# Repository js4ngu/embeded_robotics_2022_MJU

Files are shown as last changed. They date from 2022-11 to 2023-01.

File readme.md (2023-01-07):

# 2022-2학기 명지대학교 임베디드 로보틱스 수업
* 3 DOF 메뉴플레이터 설계 및 개발
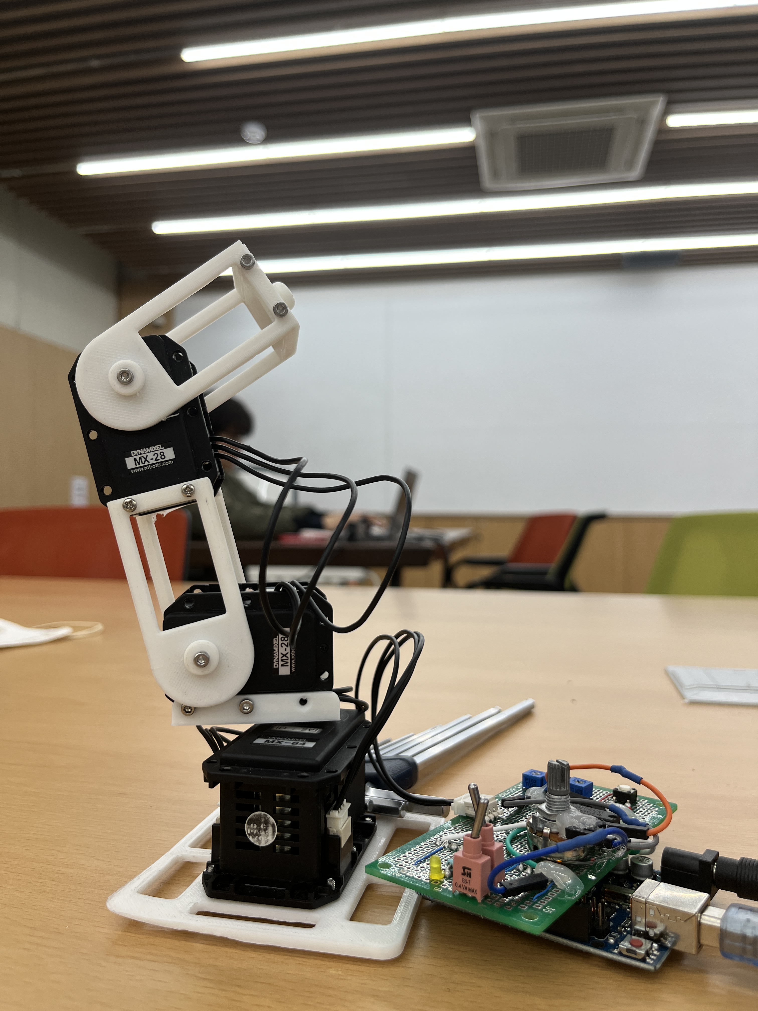
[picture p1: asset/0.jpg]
* 
* https://youtu.be/WQkYmM9BQwU
* 역기학모드
  * 직교좌표계로 좌를 입력하면 Endpoint가 해당 좌표로 이동
  * 문제를 쉽게 해석하기 위해 직교좌표계를 원통좌표계로 변환 $\phi$ 정보를 첫번째 관절에 제공
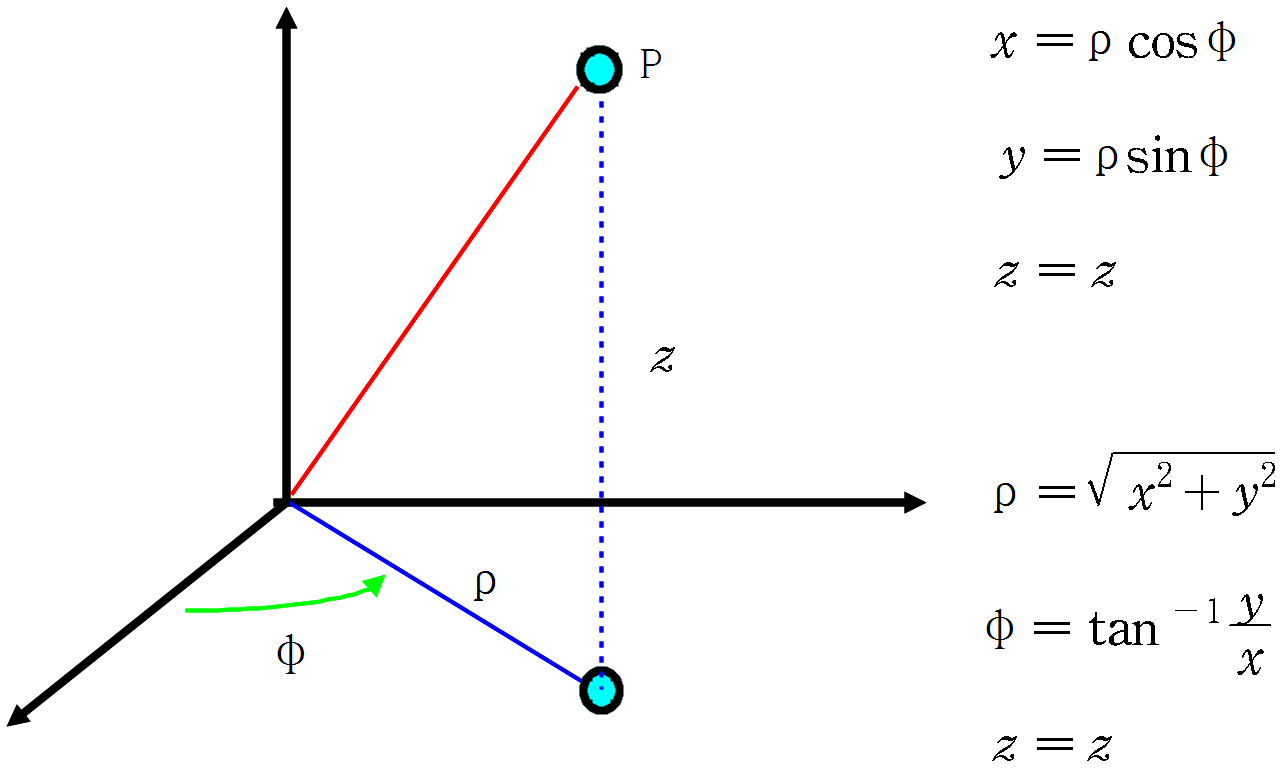
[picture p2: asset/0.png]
cord
  * 
  * $r$과 $z$로 이뤄진 2차원 평면상에서 도해적으로 해석
    * 본인은 $\rho$ 대신 $r$문자 사용
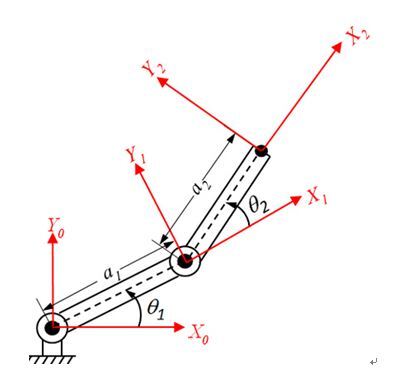
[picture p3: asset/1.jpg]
  * 
  * 결과는 아래와 같음
  * th1
  * th2
  * $\theta_1$은 $theta_2$에 dependency가 있음
  * 즉, 직교좌표계 $\rightarrow$ 원통좌표계 $\rightarrow$ $\theta_2$ $\rightarrow$ $\theta_1$ 순으로 계산해야함
  * 코드로 구현하면 아래와 같음
  * ```cpp
    void cartsia2cylinder(double x, double y, double _z){
        double cord[3];
        pi = atan2(y,x) * 57.2958;
        r = sqrt(x*x + y*y);
        z = _z;
    }

    double findTheta2(double r, double z){
        double innerSqrt = ((L1 + L2)*(L1 + L2) - (r*r + z*z))/
                            ((r*r + z*z) - (L1 - L2)*(L1 - L2));
        return 2*atan(sqrt(innerSqrt))* 57.2958;
    }

    double findTheta1(double r, double z, double th2){
        double firstTerm = atan2(z,r)*57.2958;
        double secondTerm = atan2(L2*sin(th2),(L1 + L2*cos(th2)))* 57.2958;
        return firstTerm - secondTerm;
    }
    ```
  * 여차저차 $\theta_1$, $\theta_2$ 구해서 다이나믹셀에 전해주면 끝~
* POT 모드
  * 포텐셜 미터 값 읽어서 각관절 구동~
  
 ## Report
 [[임베디드로보틱스]_6조_유종상_60171851.pdf](https://github.com/js4ngu/embeded_robotics_2022_MJU/files/10366018/_6._._60171851.pdf)

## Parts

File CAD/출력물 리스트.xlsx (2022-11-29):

Part | Required | STL Convert | G-CODE Convert | 3D printing
 |  |  |  | 1 | 2
28Tzig_50mm.par | 2 | O | O
28Tzig_50mm_right.par | 2 | O
robot_part_3.par | 2 | O
robot_part_4.par | 1 | O
robot_part_5.par | 1 | O
robot_part_6.par | 1 | O
robot_part_7.par | 1 | O
robot_part_8.par | 1 | O
robot_part_9.par | 1 | O
robot_part_10.par | 0 | O

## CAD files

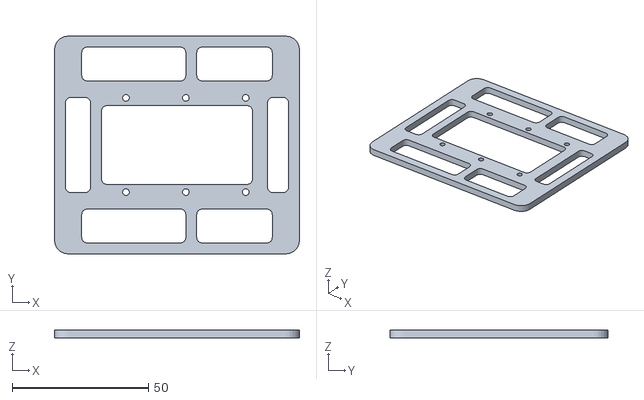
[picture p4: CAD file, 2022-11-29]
CAD/STL/robot_part_9.stl
90.0 x 80.0 x 3.00

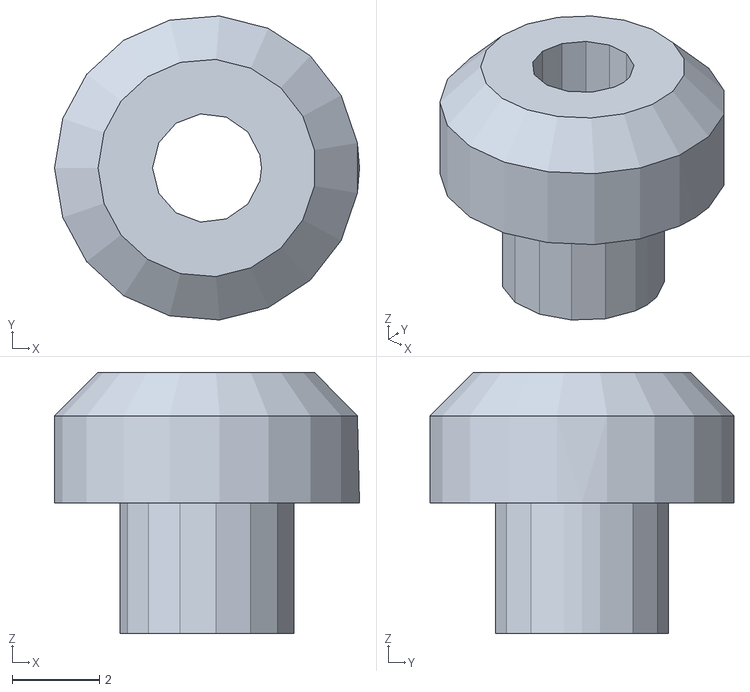
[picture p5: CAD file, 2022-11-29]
CAD/STL/robot_part_3.stl
7.00 x 6.98 x 6.00

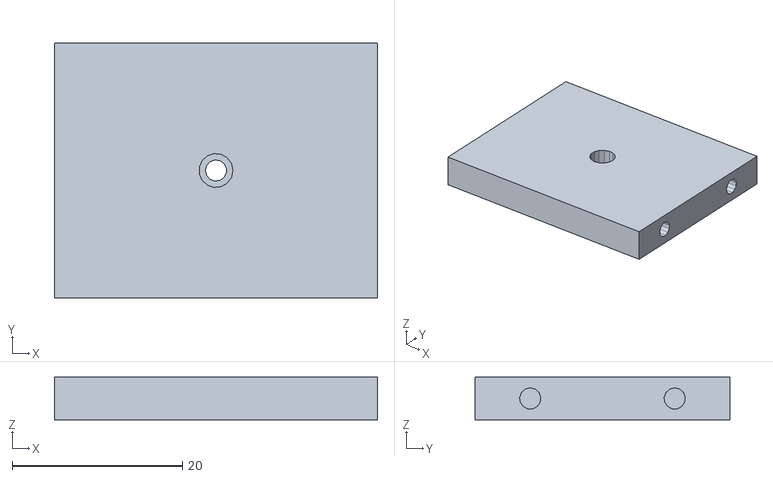
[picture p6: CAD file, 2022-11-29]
CAD/STL/robot_part_6.stl
38.0 x 30.0 x 5.00

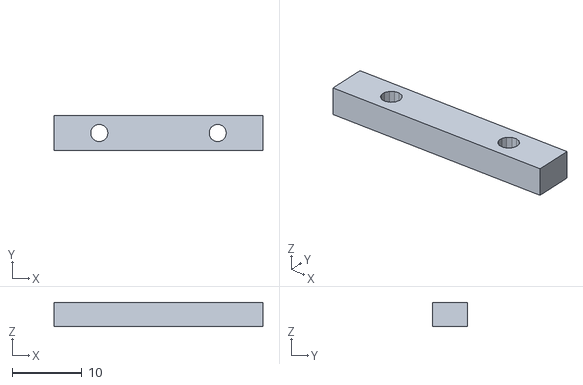
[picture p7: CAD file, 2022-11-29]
CAD/STL/robot_part_4.stl
30.0 x 5.00 x 3.50

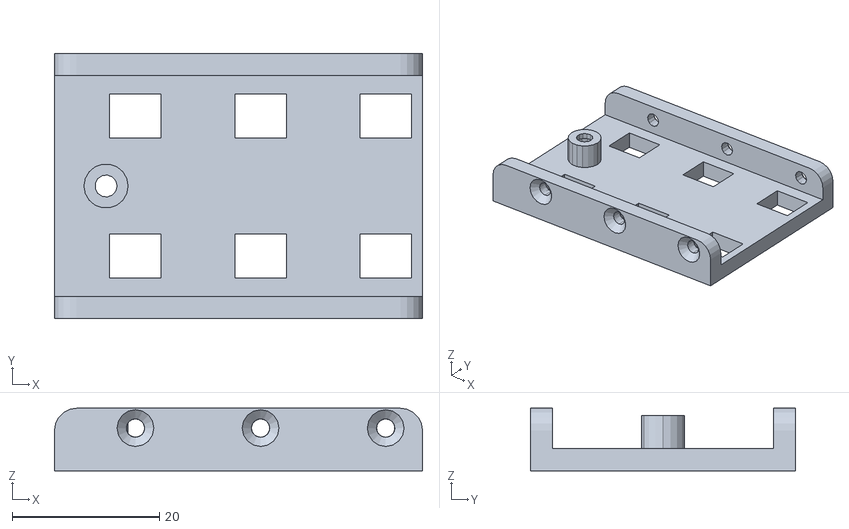
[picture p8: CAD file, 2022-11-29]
CAD/STL/robot_part_8.stl
50.0 x 36.0 x 8.50

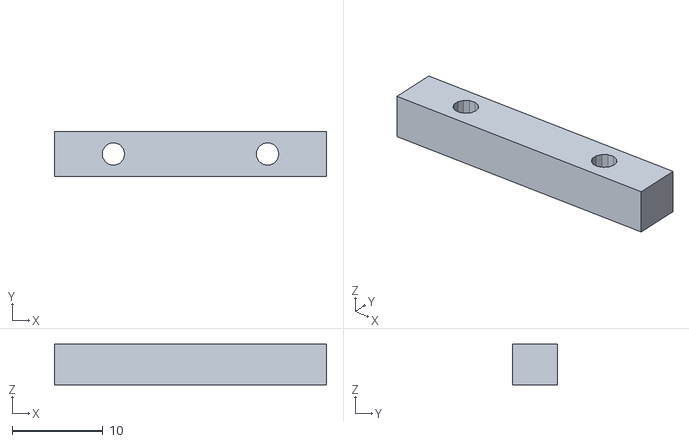
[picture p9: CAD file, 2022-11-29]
CAD/STL/robot_part_5.stl
30.0 x 5.00 x 4.50

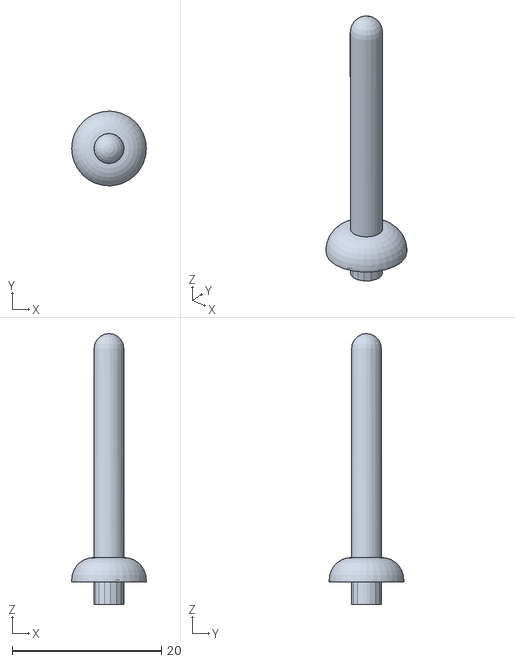
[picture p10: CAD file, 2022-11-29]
CAD/STL/robot_part_7.stl
10.0 x 10.0 x 36.3

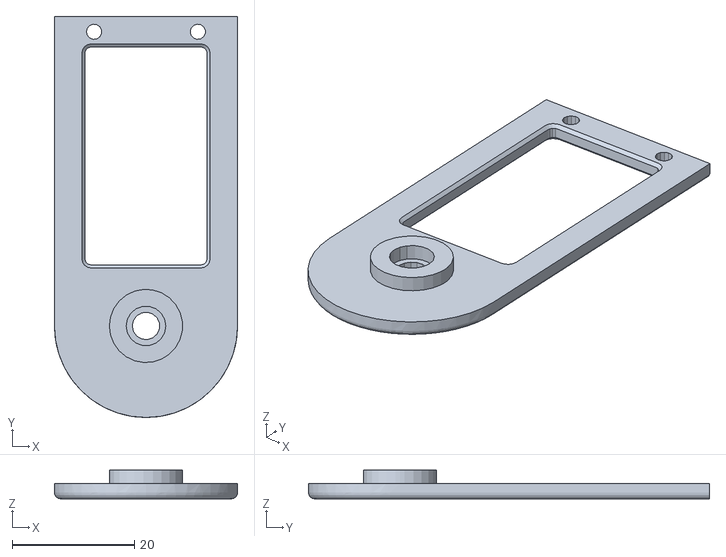
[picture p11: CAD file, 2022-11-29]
CAD/STL/28Tzig_50mm_right.stl
30.0 x 65.7 x 4.70

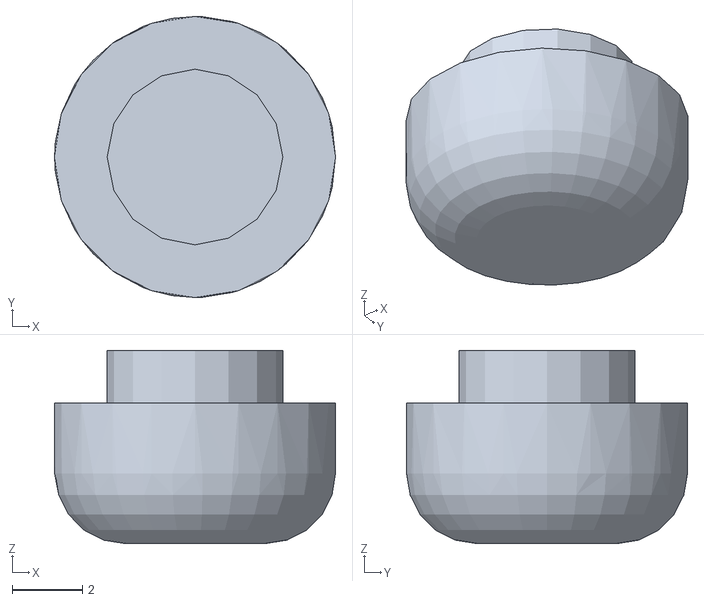
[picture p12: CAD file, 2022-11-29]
CAD/STL/robot_part_10.stl
8.00 x 8.00 x 5.50

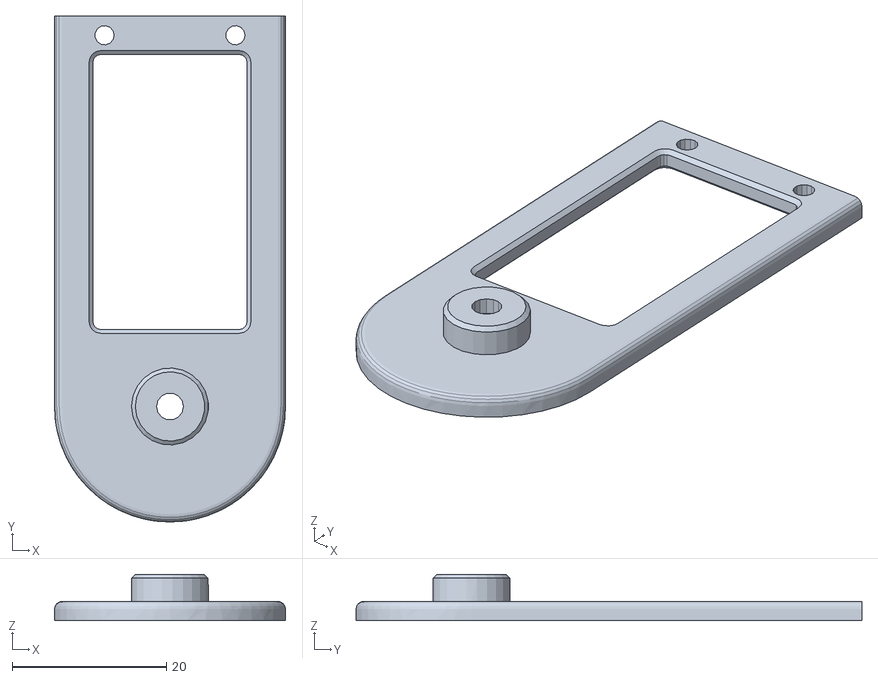
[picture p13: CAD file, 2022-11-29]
CAD/STL/28Tzig_50mm.stl
30.0 x 65.7 x 6.00

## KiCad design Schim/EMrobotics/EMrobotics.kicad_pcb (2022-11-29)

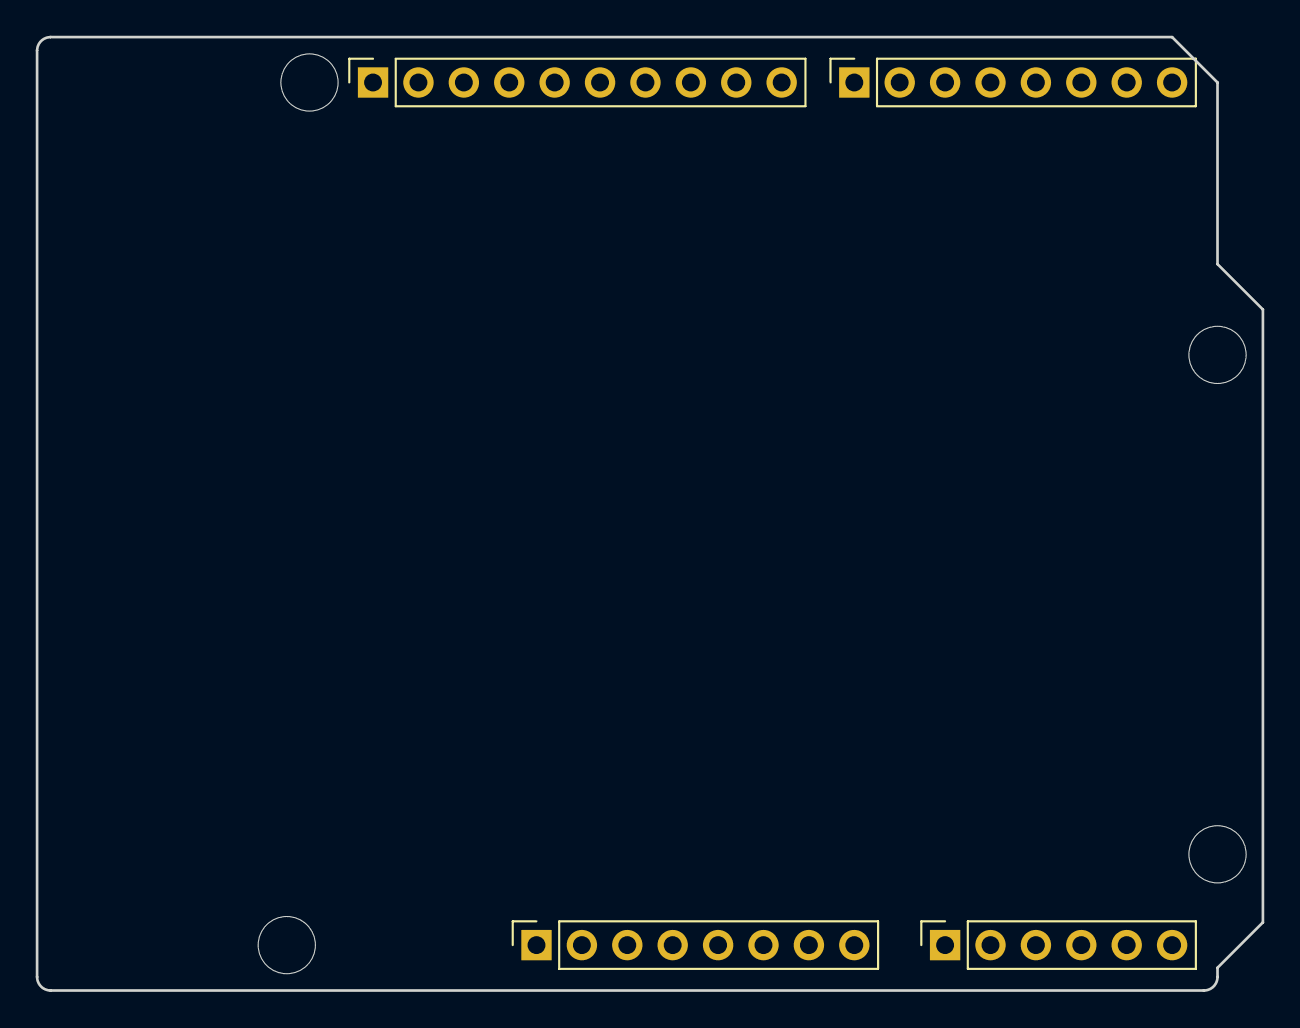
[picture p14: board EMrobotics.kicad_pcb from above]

Board: 2 copper layers, 68.6 x 53.3 mm, 8 parts (0 on the bottom side), 3 nets, no tracks yet.

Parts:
J1: Power; PinSocket_1x08_P2.54mm_Vertical
J2: Digital/PWM; PinSocket_1x10_P2.54mm_Vertical
J3: Analog; PinSocket_1x06_P2.54mm_Vertical
J4: Digital/PWM; PinSocket_1x08_P2.54mm_Vertical
MH1, MH2, MH3, MH4: MountingHole_3.2mm

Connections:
/SCL/A5: J2.1, J3.6
/SDA/A4: J2.2, J3.5
GND: J1.6, J1.7, J2.4

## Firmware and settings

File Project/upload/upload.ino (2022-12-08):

#include <stdio.h>
#include <stdlib.h>
#include <math.h>
#define L1 35
#define L2 35
#define BUFFER_SIZE 10
#define TX_Enable_pin            12  // 송신 활성화 핀
#define RX_Enable_pin            13  // 수신 활성화 핀
#define POTMODE                  0
#define INVERSEKINEMATICMODE     1
#define MOTOR_TEST_MODE          2
#define MOTOR_INIT_MODE          3
#define BOTTOM_ID                0
#define MIDDLE_ID                1
#define TOP_ID                   100
#define POT_BOTTOM               0
#define POT_MIDDLE               1
#define POT_TOP                  2
#define ERROR                    -1
typedef enum _com_mode {
    RX_MODE,
    TX_MODE
} com_mode;

// 통신 모드(송/수신)에 따른 버퍼칩 설정
void set_com_mode(com_mode mode);
// 통신 프로토콜에 체크섬 삽입
void dx_insert_checksum_byte(unsigned char *packet);
// id 설정을 위한 통신 패킷 조립
void dx_set_id(unsigned char id);
// 제어 모드 설정
// 정방향과 역방향 최대 각도에 따라 바퀴모드나 관절모드로 설정됨
// 바퀴모드: 모두 0으로 설정
// 관절모드: 0~360(0xfff)로 설정
void dx_set_control_mode(unsigned char id, unsigned char cw_angle_limit[2], unsigned char ccw_angle_limit[2]);
// 위치제어용 패킷 조립
void dx_tx_packet_for_position_control(unsigned char id, unsigned char goal_pos[2]);
int readModeSW();
void potMode();
void inverseMode();
void cartsia2cylinder(float x, float y, float _z);
float findTheta2(float r, float z);
float findTheta1(float r, float z, float th2);
void findInverseKinematic(float x, float y, float z);
bool toggleSW();
unsigned char topPacket(int REF);
unsigned char bottomPacket(int REF);

unsigned char ref_0[2];
unsigned char ref_1[2];
unsigned char ref_2[2];
int potVal[3];
float cartsianCord[3];
float r, pi, z;
int motorDeg[3];
char buf[BUFFER_SIZE];
int stateMainFSM;

void setup() {
    Serial.begin(57600);  // 통신 속도
    pinMode(TX_Enable_pin, OUTPUT); //TX Enable
    pinMode(RX_Enable_pin, OUTPUT); //RX Enable
    pinMode(2, OUTPUT);
    pinMode(5, OUTPUT);
    pinMode(6, OUTPUT);
    pinMode(8, OUTPUT);
    pinMode(9, INPUT);
    pinMode(10, INPUT);

    unsigned char cw_angle_limit[2];
    unsigned char ccw_angle_limit[2];

    cw_angle_limit[0] = 0x00;
    cw_angle_limit[1] = 0x00;
    ccw_angle_limit[0] = 0xFF;
    ccw_angle_limit[1] = 0xFF;  

    dx_set_control_mode(254, cw_angle_limit, ccw_angle_limit);
    digitalWrite(2, HIGH);
    digitalWrite(6, HIGH);
    digitalWrite(8, HIGH);
    delay(1);
}

void loop() {
    switch (readModeSW()) {
    case POTMODE:
        potMode();
        break;

    case INVERSEKINEMATICMODE:
        inverseMode();
        break;

    case MOTOR_TEST_MODE:
        ref_0[0] = 0x00;
        ref_0[1] = 0x10;
        dx_tx_packet_for_position_control(BOTTOM_ID, ref_0);
        delay(1000);
        dx_tx_packet_for_position_control(MIDDLE_ID, ref_0);
        delay(1000);
        dx_tx_packet_for_position_control(TOP_ID, ref_0);
        delay(1000);
        ref_0[0] = 0x00;
        ref_0[1] = 0x00;
        dx_tx_packet_for_position_control(BOTTOM_ID, ref_0);
        delay(1000);
        dx_tx_packet_for_position_control(MIDDLE_ID, ref_0);
        delay(1000);
        dx_tx_packet_for_position_control(TOP_ID, ref_0);
        delay(1000);
        break;

    case MOTOR_INIT_MODE:
        ref_0[0] = 0x00;
        ref_0[1] = 0x08;
        dx_tx_packet_for_position_control(BOTTOM_ID, ref_0);
        delay(1000);
        dx_tx_packet_for_position_control(MIDDLE_ID, ref_0);
        delay(1000);
        dx_tx_packet_for_position_control(TOP_ID, ref_0);
        delay(1000);
        while(1);
    }
}

int readModeSW(){
    bool modeSW = digitalRead(9);
    if(modeSW == 0){
        digitalWrite(5, HIGH);
        return POTMODE;
    }
    else if(modeSW == 1){
        digitalWrite(5, LOW);
        return INVERSEKINEMATICMODE;
    }
    else
        return ERROR;
}

bool toggleSW(){
    static bool prev_btn;
    static bool current_btn;
    current_btn = digitalRead(10);
    if ( (prev_btn ^ current_btn) == 1){
        prev_btn = current_btn;
        Serial.println("SW");
        return 1;
    }
    else{
        prev_btn = current_btn;
        return 0;
    }
}

void potMode(){
    static int state = 0;
    switch (state)
    {
    case 0:
        while(1){
            potVal[POT_BOTTOM] = analogRead(A2)*4;
            Serial.print("POT_BOTTOM : ");
            Serial.println(potVal[POT_BOTTOM]);
            if (toggleSW() == 1) {
                state = 1;
                break;
            }
        }
        break;
    case 1:
        while(1){
            potVal[POT_MIDDLE] = analogRead(A2)*4;
            Serial.print("POT_MIDDLE : ");
            Serial.println(potVal[POT_MIDDLE]);
            if (toggleSW() == 1) {
                state = 2;
                break;
            }
        }
        break;
    case 2:
        while(1){
            potVal[POT_TOP] = analogRead(A2)*4;
            Serial.print("POT_TOP : ");
            Serial.println(potVal[POT_TOP]);
            if (toggleSW() == 1) {
                state = 3;
                break;
            }
        }
        break;
    case 3:
        Serial.print(potVal[POT_BOTTOM]);
        Serial.print("\t");
        Serial.print(potVal[POT_MIDDLE]);
        Serial.print("\t");
        Serial.println(potVal[POT_TOP]);
        state = 4;
        break;

    case 4:
        motorDeg[POT_BOTTOM] = potVal[POT_BOTTOM];
        motorDeg[POT_MIDDLE] = potVal[POT_MIDDLE];
        motorDeg[POT_TOP]    = potVal[POT_TOP];

        ref_0[0] = bottomPacket(motorDeg[0]);
        ref_0[1] = topPacket(motorDeg[0]);
        dx_tx_packet_for_position_control(BOTTOM_ID, ref_0);
        delay(1000);
        ref_1[0] = bottomPacket(motorDeg[1]);
        ref_1[1] = topPacket(motorDeg[1]);
        dx_tx_packet_for_position_control(MIDDLE_ID, ref_1);
        delay(1000);
        ref_2[0] = bottomPacket(motorDeg[2]);
        ref_2[1] = topPacket(motorDeg[2]);
        dx_tx_packet_for_position_control(TOP_ID, ref_2);
        delay(1000);

        while (1) {
            if (toggleSW() == 1) {
                state = 0;
                break;
            }
        }    
        break;
    }
}

void set_com_mode(com_mode mode) {

  if (mode == RX_MODE)
  {
    // 비활성화 먼저 수행하여 동시에 활성화 되는 순간을 방지
    digitalWrite(TX_Enable_pin, LOW); // TX disable
    digitalWrite(RX_Enable_pin, HIGH); // RX Enable
  }
  else
  {
    // 비활성화 먼저 수행하여 동시에 활성화 되는 순간을 방지
    digitalWrite(RX_Enable_pin, LOW); // RX disable
    digitalWrite(TX_Enable_pin, HIGH); // TX Enable
  }
}
void dx_insert_checksum_byte(unsigned char *packet) {

  unsigned char i;
  unsigned char checksum_pt;
  unsigned char checksum;
  unsigned char packet_length;

  packet_length = packet[3];  // 3번 바이트에 패킷 길이가 저장되어 있음
  checksum_pt = packet_length + 3;

  checksum = 0x00;
  for (i = 2; i < checksum_pt; i++) {
    checksum += packet[i];
  }
  packet[checksum_pt] = ~checksum;

}
void dx_set_id(unsigned char id) {
  unsigned char packet[8];
  unsigned char i;

  packet[0] = 0xFF;
  packet[1] = 0xFF;
  packet[2] = 0xFE;
  packet[3] = 0x04;
  packet[4] = 0x03;
  packet[5] = 0x03;
  packet[6] = id;

  dx_insert_checksum_byte(packet);

  set_com_mode(TX_MODE); // 송신 모드로 설정
  for (i = 0; i < 8; i++) {
    Serial.write(packet[i]);
  }

  // 송신완료시까지 블록
  while ( !(UCSR0A & (1 << TXC0)) ) {
    __asm__("nop\n\t"); // no operation
  }

  set_com_mode(RX_MODE); // 수신 모드로 설정

}
void dx_set_control_mode(unsigned char id,
                         unsigned char cw_angle_limit[2],
                         unsigned char ccw_angle_limit[2]) {

  unsigned char packet[11];
  unsigned char i;

  packet[0] = 0xFF;
  packet[1] = 0xFF;
  packet[2] = id;
  packet[3] = 0x07;
  packet[4] = 0x03;
  packet[5] = 0x06;
  packet[6] = cw_angle_limit[0];
  packet[7] = cw_angle_limit[1];
  packet[8] = ccw_angle_limit[0];
  packet[9] = ccw_angle_limit[1];
  dx_insert_checksum_byte(packet);

  set_com_mode(TX_MODE); // 송신 모드로 설정
  for (i = 0; i < 11; i++) {
    Serial.write(packet[i]);
  }

  // 송신완료시까지 블록
  while ( !(UCSR0A & (1 << TXC0)) ) {
    __asm__("nop\n\t"); // no operation
  }

  set_com_mode(RX_MODE); // 수신 모드로 설정

}
void dx_tx_packet_for_position_control(unsigned char id, unsigned char goal_pos[2]) {
  
  unsigned char packet[11];
  unsigned char i;

  packet[0] = 0xFF;
  packet[1] = 0xFF;
  packet[2] = id;
  packet[3] = 0x07;
  packet[4] = 0x03;
  packet[5] = 0x1E;
  packet[6] = goal_pos[0];
  packet[7] = goal_pos[1];
  packet[8] = 0x00;
  packet[9] = 0x00;
  dx_insert_checksum_byte(packet);

  set_com_mode(TX_MODE); // 송신 모드로 설정
  for (i = 0; i < 11; i++) {
    Serial.write(packet[i]);
  }

  // 송신완료시까지 블록
  while ( !(UCSR0A & (1 << TXC0)) ) {
    __asm__("nop\n\t"); // no operation
  }
  
  set_com_mode(RX_MODE); // 수신 모드로 설정
}

void findInverseKinematic(float x, float y, float z){
    cartsia2cylinder(x, y, z);
    float theta2 = findTheta2(r,z);
    float theta1 = findTheta1(r,z,theta2);
    motorDeg[0] = int(pi*11);
    motorDeg[1] = int(theta1*11);
    motorDeg[2] = int(theta2*11);
}

void cartsia2cylinder(float x, float y, float _z){
    float cord[3];
    pi = atan2(y,x) * 57.2958;
    r = sqrt(x*x + y*y);
    z = _z;
}

float findTheta2(float r, float z){
    float innerSqrt = ((L1 + L2)*(L1 + L2) - (r*r + z*z))/
                        ((r*r + z*z) - (L1 - L2)*(L1 - L2));
    return 2*atan(sqrt(innerSqrt))* 57.2958;
}

float findTheta1(float r, float z, float th2){
    float firstTerm = atan2(z,r)*57.2958;
    float secondTerm = atan2(L2*sin(th2),(L1 + L2*cos(th2)))* 57.2958;
    return firstTerm - secondTerm;
}

unsigned char bottomPacket(int REF){
    return REF % (16*16);
}

unsigned char topPacket(int REF){
  return (REF/(16*16))%(16*16);
}

void inverseMode(){
    char inCom;
    static int state = 0;
    switch (state)
    {
    case 0:
        for (int i = 0; i < 3;  i++) {
            Serial.print("INPUT (since 3Sec) : \n");
            delay(3000);
            if (Serial.available()){
                cartsianCord[i] = Serial.parseInt();
            }
        }
        while (1) {
            char inCOme;
            Serial.print("Press 'a' to start\n");
            if (Serial.available()){
                inCOme = Serial.read();
            }
            if (inCOme == 'a') {
                break;
            }
        }
        state = 1;
        break;
    
    case 1:
        findInverseKinematic(cartsianCord[0], cartsianCord[1], cartsianCord[2]);
        ref_0[0] = bottomPacket(motorDeg[0]);
        ref_0[1] = topPacket(motorDeg[0]);
        dx_tx_packet_for_position_control(BOTTOM_ID, ref_0);
        delay(1000);
        ref_1[0] = bottomPacket(motorDeg[1]);
        ref_1[1] = topPacket(motorDeg[1]);
        dx_tx_packet_for_position_control(MIDDLE_ID, ref_1);
        delay(1000);
        ref_2[0] = bottomPacket(motorDeg[2]);
        ref_2[1] = topPacket(motorDeg[2]);
        dx_tx_packet_for_position_control(TOP_ID, ref_2);
        delay(1000);
        state = 2;
        break;
    case 2:
        while (1) {
            char inCOme;
            Serial.print("Press 'a' to restart\n");
            if (Serial.available()){
                inCOme = Serial.read();
            }
            if (inCOme == 'a') {
                state = 0;
                break;
            }
        }
    }
}

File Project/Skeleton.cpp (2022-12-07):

#include <stdio.h>
#include <math.h>
#define L1 10
#define L2 10
#define POTMODE 0
#define INVERSEKINEMATIC 1
#define POT_X 0
#define POT_Y 1

void cartsia2cylinder(double x, double y, double _z);
double findTheta2(double r, double z);
double findTheta1(double r, double z, double th2);
void findInverseKinematic(double x, double y, double z);
void potRead();
void potVal2motorDeg();
bool modeSW();
void FSM(bool mode);
void InverseKinematicMode();
void potMode();

double cartsianCord[3];
double r, pi, z;
double motorDeg[3];
int potVal[2];
bool SW;

int main(){
    FSM(modeSW());
}

void FSM(bool mode){
    if (mode == INVERSEKINEMATIC) {
        InverseKinematicMode();
    }
    else if (mode == POTMODE) {
        potMode();
    }
}

void InverseKinematicMode(){
    scanf("%lf %lf %lf", &cartsianCord[0], &cartsianCord[1], &cartsianCord[2]);
    findInverseKinematic(cartsianCord[0], cartsianCord[1], cartsianCord[2]);
    for (size_t i = 0; i < 3; i++)
        printf("%lf\t", motorDeg[i]);
}

void potMode(){
    potRead();
    potVal2motorDeg();
}

bool modeSW(){
    if (digiatlRead(6) == 1)
        return POTMODE;
    else
        return INVERSEKINEMATIC;
}

void potRead(){
    SW = digitalRead(A5);
    potVal[POT_X] = analogRead(A4);
    potVal[POT_Y] = analogRead(A4);
}

void potVal2motorDeg(){
    for (int i = 0; i < 3; i++) {
        motorDeg[i] = map(potVal[i], 0, 1024, 0, 360);
    }
    for (size_t i = 0; i < 3; i++)
        printf("%lf\t", motorDeg[i]);
}

void findInverseKinematic(double x, double y, double z){
    cartsia2cylinder(x, y, z);
    double theta2 = findTheta2(r,z);
    double theta1 = findTheta1(r,z,theta2);
    motorDeg[0] = pi;
    motorDeg[1] = theta1;
    motorDeg[2] = theta2;
}

void cartsia2cylinder(double x, double y, double _z){
    double cord[3];
    pi = atan2(y,x) * 57.2958;
    r = sqrt(x*x + y*y);
    z = _z;
}

double findTheta2(double r, double z){
    double innerSqrt = ((L1 + L2)*(L1 + L2) - (r*r + z*z))/
                        ((r*r + z*z) - (L1 - L2)*(L1 - L2));
    return 2*atan(sqrt(innerSqrt))* 57.2958;
}

double findTheta1(double r, double z, double th2){
    double firstTerm = atan2(z,r)*57.2958;
    double secondTerm = atan2(L2*sin(th2),(L1 + L2*cos(th2)))* 57.2958;
    return firstTerm - secondTerm;
}

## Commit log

2022-11-29 CAD & EDA DONE
    [28Tzig_50mm.stl, 28Tzig_50mm_right.stl, EMrobotics.kicad_pcb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]
2022-12-03 역기구학 계산
2022-12-03 역기구학 함수화
2022-12-06 리드미 화살표 수정
2022-12-07 일단 모터는 돔 SW에 따른 mode 변경 됨 POT 회로 이슈
2022-12-07 계산code OK
2022-12-08 pause기능구현
